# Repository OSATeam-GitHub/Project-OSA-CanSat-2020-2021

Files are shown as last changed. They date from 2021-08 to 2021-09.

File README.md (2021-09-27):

#  Project OSA

OSA a is minisatellite/ space probe the size of a can designed to participate in the ESA CanSat 2021 competition 🛰️📡. Our project is called OSA (in Polish “Opadający Satelita Atmosferyczny” is loosely translated into “Falling Atmospheric Satellite”) and team - [OSATeam](https://www.osacan.eu/)

OSA is desgined to carry out reasearches while falling in the atmospehere. Space probe can be deployed from drone, rocket or droped from certain altitude. Parachute guarantees safe landing. Primarily device measures air temperature, pressure, humidity and send it via LoRa radio to the ground station. This data is used onboard sattelite to calculate live altitude. 

The main aim for OSA is to collect five air samples🧪 for later analysis. It is done by custom-designed mechanism, that injects needle to autosealing sterile containers and pump air sample into it. 

Among other OSA has built-in GPS so after lunch it can be found easily.

CS_OSATeam2

## Tabele of contents
* [Mechanical design](#mechanical-design)
* [Electronic design](#electronic-design)
* [OSA software](#osa-software)
* [Contact](#contact)
* [Licence](#licence)
## Mechanical design
Mechanical was designed in fusion 360. The full project is available to watch with this link:
https://a360.co/3AG3GMY. 
All parts which should be 3D printed are also available above. You should use precise printer. To print them we used high-quality PLA. Inaacuracy will yield in device inoperatavity. 

### Sting System
System injects needle into container using gear and slider powered by servomechanism. Then pump inflates atmosphere into the container. In fact there is to need to use pump due to fact containers are underpressure, although puting pump into system will increase concentartion of gases. Then upper part of sting system is rotated by carousele. 



### Carousele
The carousel is designed to turn the servo and sting. It uses a stepper motor and three gears (ratio 1:1:1). The
motor does not have a centered shaft, therefore a gear system consisting of three gears has been printed on a 3D
printer. Servo gear is located in the middle and it holds the servo. On one side there is motor gear that is attached
to the [28BYJ-48 stepper motor](https://botland.com.pl/silniki-krokowe/12807-silnik-krokowy-z-przekladnia-28byj-48-5v-01a-003nm-ze-sterownikiem-uln2003.html). On the opposite side, there is support gear that makes the mechanism work with lower
backlash. Carusele is part of main-base body. It might be challenging to print therefor we additionaly added splited main-base part. Printing spearetly should be easier, after printing that way the prats should be glued togather.
Servo gear is printed in place with the base of the case as one part. It is mounted on the round body, so
it holds together. Support gear is printed as a separate part. While the base is printing the printer should be stoped at the right
height so the support gear could be manually added ( the stoping point can be set in slicer ).

karuzela napisy

### Servo mechanism
The servo mechanism converts the rotation of the motor into linear movement of the needle therefore it can be injected into the test tube.
The blocker part is additionally added to help the needle stay in place.



### Main casing body and electronic case
Both the main casing body ( main-mid ) and the electronic case are designed to be printed without any supports. They don't require as high precision as the carousel does.

## Electronic design
OSA is powered by the CanSat kit, therefore it’s fully compatible with Arduino m0. Full CanSat kit documentation can be found on the ESERO Polska page in the statute, or right [here](https://github.com/CanSatKit/Documentation). On to the mainboard, you should sold GPS module as well as the  1/2 wave long antenna. [This](https://www.changpuak.ch/electronics/yagi_uda_antenna_DL6WU.php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) calculator may be useful. 

Currently, we are working on a new PCB board for OSA. We will upload the design with the scheme soon.

OsaCan-1

### Ground station hardware
OSA ground station is simply the CanSat kit board connected with a yagi directional antenna. The mainboard should be connected by USB with PC or laptop.
It will work with any antenna which fulfils requirments (the closer to requitments the better signal:

- Frequency     :  433  MHz
- Wavelength    :  693  mm
- Rod Diameter  :  10  mm
- Boom Diameter :  20  mm
- Boom Length   :  238  mm
- d/lambda      :  0.014    ( min.: 0.002 , max.: 0.01 )
- D/lambda      :  0.029    ( min.: 0.01 , max.: 0.05 )
- Elements      :  3
- Gain          :  5.23 dBd (approx.)
- Reflector Length   : 334 mm
- Reflector Position :  0 mm
- Dipole Position    : 166 mm
- Director #1 Position : 218 mm ,  Length : 315 mm
- Distance Dipole - Dir. #1 : 52 mm 

[yagi antenna calculator](https://www.changpuak.ch/electronics/yagi_uda_antenna_DL6WU.php)

## OSA software
OSA OS is Arduino based. To make the code clean we wrote a library for controlling all OSA systems. 

Before launch, when OSA is turned on it will take measurements and calculation to establish ground altituted. Until detecting the opening of the parachute OSA will stay in the rest position. It means that the needle will be hidden between two probes so it takes less space. After detecting the opening of the parachute OSA waits about a second to stabilize and then sets current altitude as final altitude. Then it calculates five intervals on which it’s supposed to take the samples. 

Independently OSA takes measurements from all sensors every second, send it via radio and save it on SD card. Excluding pressure, temperature, humidity OSA equipped with a sensor that measures the pressure inside the pipe connected with the needle. According to that pressure we know whether the probe was taken or not. If for some reason any of the samples wasn’t taken, after taking all others OSA will come back and repeat taking those samples. OSA sends various data about the so not only do we know whether the sample was taken or not, but also exactly the altitude it started and finished taking. Also, the altitude at which the parachute was opened is saved.

OSA encodes data which is send via radio, otherwise buffor would have stucked. 

## Contact
📫 We are opened to suggestions and collaboration. Contact us!
- https://www.facebook.com/osacan.eu/
- https://www.instagram.com/osateam_cansat/
- osacansat@gmail.com
- @OSATeam_CanSat

## Licence
Copyright (C)  2020 Project OSA.

This project is free software and hardware: you can redistribute it and/or modify
    it under the terms of the GNU General Public License as published by
    the Free Software Foundation, either version 3 of the License, or
   any later version.

   This program is distributed in the hope that it will be useful,
    but WITHOUT ANY WARRANTY; without even the implied warranty of
    MERCHANTABILITY or FITNESS FOR A PARTICULAR PURPOSE.  See the
    GNU General Public License for more details.

   You should have received a copy of the GNU General Public License
    along with this program.  If not, see <https://www.gnu.org/licenses/>.
    
<!---
OSATeam-GitHub/OSATeam-GitHub is a ✨ special ✨ repository because its `README.md` (this file) appears on your GitHub profile.
You can click the Preview link to take a look at your changes.
--->

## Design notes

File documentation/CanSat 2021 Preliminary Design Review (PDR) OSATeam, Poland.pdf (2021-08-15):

## CanSat 2021 Preliminary Design Review (PDR) OSATeam, Poland

VIII Prywatne Akademickie Liceum Ogólnokształcące w Krakowie

TABLE OF CONTENTS

CHANGELOG | 2
INTRODUCTION | 2
Team presentation | 2
Team organisation and roles | 2
Mission objectives | 3
Cansat Description | 3
Mission overview | 4
Mechanical/structural design | 5
Carousel | 5
Servomechanism | 5
Pumping System | 6
Probes | 6
Casing | 7
Electrical design | 7
General architecture | 7
Primary mission devices | 8
Secondary mission devices | 8
Electrical scheme | 9
Power supply | 10
Communication system | 10
Transceiver part of OSACan | 10
Ground Receiving Station | 10
Software design | 12
Recovery system | 14
Ground support Equipment | 15
Laptop | 15
Ground receiving station | 15
Chromatograph | 15
Basic set of tool and spare parts | 15
TEST CAMPAIGN | 15
Primary mission tests | 15
Measurement tests | 15
Data download tests | 16
Sending/receiving tests | 16
Secondary mission tests | 16
Measurement tests | 16
Sting System tests | 16
Endurance tests | 16
SD card test: | 17
Tests of recovery system | 17
Communication system range tests | 17
Energy budget tests | 17
Test equipment: | 17
Project Planning | 18
Time schedule | 18
Task list | 19
Resource cost estimation | 19
Budget | 19
External support | 20
Outreach programme | 20
CanSat characteristics | 20

### 1. CHANGELOG

- One member of OSATeam resigned. The team has now 4 members and faculty advisor.

### 2. INTRODUCTION

2.1. Team presentation
OSA (in Polish “Opadający Satelita Atmosferyczny” is loosely translated into “Falling Atmospheric Satellite”) is a project of 4 students from one class out from one of Cracow’s high schools, who decided that, apart from school, they wanted to take on a serious project. Together, they decided to take part in the CanSat competition.
2.2. Team organisation and roles

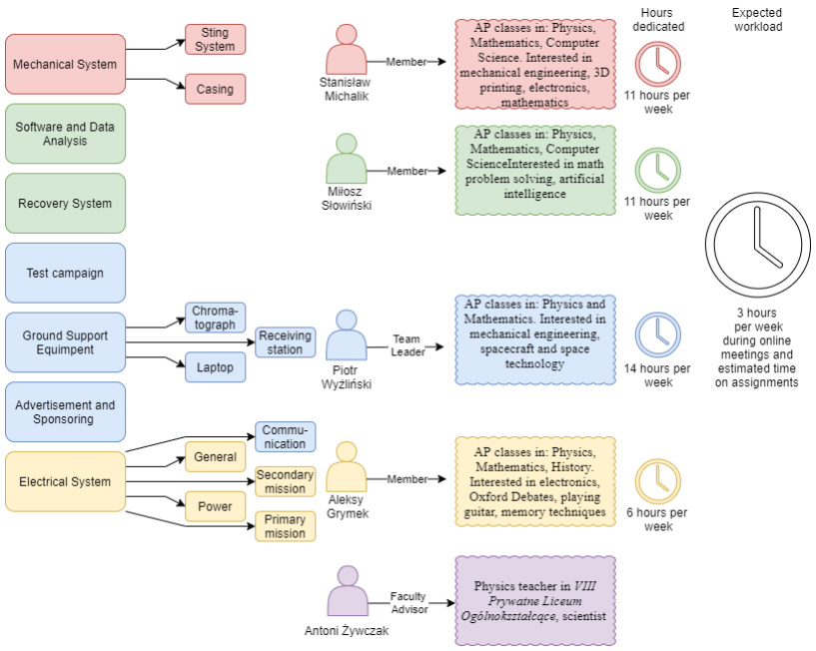
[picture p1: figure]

figure 1

2.3. Mission objectives
CanSat's primary mission is to measure the pressure and the temperature of the atmosphere during its descent and to send those measurements to a radio ground station every second. These data will be simultaneously saved in the local CanSat's memory so that it can be analyzed after the satellite lands.
The data from the primary mission will be used to calculate the height from which the CanSat will have been dropped and to calculate live altitude, and hence the speed and the time of the descent. Based on these calculations, there will be adjusted times when the next atmosphere samples are going to be collected (The first sample will be taken when the descent begins. We plan to decide if it will be detected by an accelerometer or by a different device)

The satellite will also provide the GPS location, necessary to locate CanSat after landing. Additional data related to the measurement process itself will be collected at the time of sampling, that is recording initial pressure in tanks, final pressure, filling time of tanks and diagnostic data of the filling mechanism. After analysis, this data will be used to control the filling process. At least 6 atmospheric sample containers are expected to be filled and delivered to ground, and process related data recorded.

The second mission was inspired by information from a recent Venus study, which detected phosphine that could indicate that there was life on this planet. OSATeam wants to test the Earth's atmosphere sampling system so that later a similar solution could be applied to a real mission.

The purpose of our second mission is to show that it is possible to collect samples without building satellites equipped with expensive and heavy research equipment, instead, samples can be effectively collected to be analyzed in an external specialized laboratory. Instead of investing in satellites with multiple sensors, you can invest in building many cheap satellites that collect valuable material for later analysis. The mission aims to demonstrate that this is realistic and that samples can be collected and safely delivered this way.

To ensure the success of the mission, the following goals must be met:

- Recovery system: the parachute must open and ensure a safe CanSat landing
- Electronic system and mechanical structure must work: after flight conditions (rocket acceleration),during descent (changes in pressure, temperature, humidity) and survive landing (impact)
- Sampling system: it must be hermetic, keep the tanks ariditile until sampling, it must not be damaged,
- Communication system: must ensure at least one-way communication (satellite -> ground station) during the flight and after landing,
- Software: must correctly implement the assumed algorithm, save all delivered data and send it by radio.
- Power supply system: must be safe, the energy reserve must be sufficient for the assumed number of working hours.

Optionally, samples collected during the tests will be tested for their composition in external laboratories. The analysis of the Earth's atmosphere could, for example, show that air pollutants (carbon dioxide, methane, ozone, freons, microplastics) can be detected in the air not only at the Earth's surface, and that the amount of pollutants varies depending on air humidity, altitude.

### 3. CANSAT DESCRIPTION

3.1. Mission overview
The OSACan is designed to be launched and dropped from a rocket or drone from an altitude of 500-2500 meters. After equalizing the forces, CanSat should drop at a speed of about 6 meters per second. The most important task of CanSat is to collect atmospheric samples into sealed containers while falling, using a sampling and filling mechanism at various heights. The samples are meant to be safely delivered to Earth, which requires proper protection of the probes against damage or leakage.

CanSat will descend on a parachute that will expand spontaneously as soon as it is dropped out of a rocket or a drone.

The satellite will be equipped with sensors to measure the parameters of the atmosphere outside the satellite (pressure, temperature and air humidity) and the parameters of the collected samples (pressure in the tank). The on-board computer will be responsible for the acquisition of data from sensors, their recording on the SD card and control of the radio communication system. It will also be responsible for starting and checking the air filling system for containers.

The radio communication system is designed to send these data at least once a second using a radio transmitter to the ground station, both during descent and after landing.

The GNSS module connected to the on-board computer will provide information about the current CanSat position based on the reception of GPS, Galileo or Glonass signals. The signal will be transmitted for at least 5 hours to make it easier to find CanSat after landing.

The Mechanical Subsystem (sampling and probe filling) is a key element of the second mission. A special sting system has been designed to fulfil the purpose of filling. An atmosphere sample at a certain altitude will be sucked from the outside of the CanSat by a gas pump. The gas, compressed to about 0.5 atm, will be forced into the vacuum tube by means of a needle piercing the sealed stopper. Several test tubes will be arranged around the CanSat circumference so that samples at atmospheres of different heights can be collected. In order to fill the next tube, a rotating system (the so-called carousel) was designed, driven by a stepper motor. The vertical position of the needle will be servo-controlled. The moment the tube is full will be identified by the pressure sensor. The mechanical subsystem is controlled by the Microcontroller Subsystem based on CanSat Kit pcba and additional pcba shield. All are powered by battery and Power Supply System. The microcontroller subsystem sends data to Ground Receiving Station using the LoRa radio module. Block diagram (figure 2) (https://drive.google.com/file/d/1fHhHfOO-vB5NrV_i7cEuDcGI7dE_luFc/view?usp=sharing) presents the proposed architecture of the whole system.

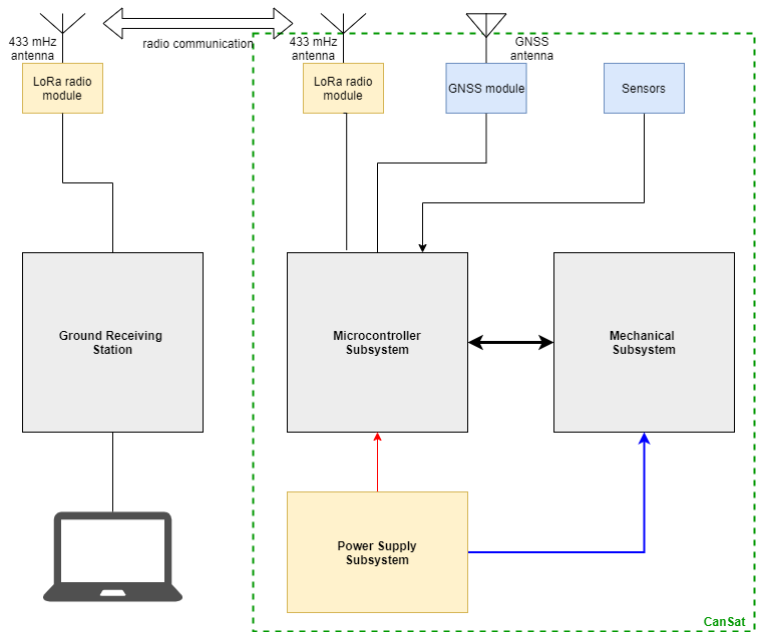
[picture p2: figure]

figure 2 (https://drive.google.com/file/d/1fHhHfOO-vB5NrV_i7cEuDcGI7dE_luFc/view?usp=sharing)

3.2. Mechanical/structural design

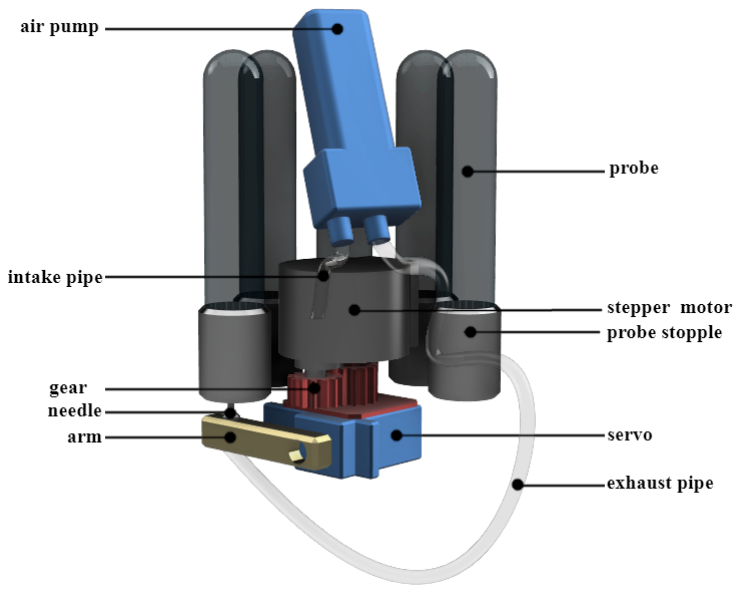
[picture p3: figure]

Figure 3 presents the Sting System. A pump will be used to collect air samples. Its inlet will lead to the outside of the CanSat and its outlet will lead to the needle. The needle will be driven into the test tubes by a servo with a special arm. To fill another tube, the servo will be rotated by a stepper motor.

← figure 3

3.2.1. Carousel
The carousel (figure 4) is designed to turn the servo. It uses a stepper motor and a gear. The motor does not have a centered shaft, therefore a gear consisting of two gears will be printed on a 3D printer.
28BYJ-48 stepper motor (https://botland.com.pl/pl/silniki-krokowe/3480-silnik-krokowy-z-przekladnia-28byj-48-5v-01a-003nm-ze-sterownikiem-uln2003-5903351241458.html) (figure 5): It was chosen due to the fact that it is the smallest stepper motor on the market with low voltage supply in a reasonable price range in the shape of a cylinder.
- Supply voltage: 5 VDC
- Current consumption per coil: 100 mA
- Number of phases: 4
- Gear: 64: 1
- Number of steps per full revolution: 64
- Rotation angle per step: 5.625 °
- Torque: 0.3 kg * cm (0.03 Nm)
- Frequency: 100Hz
- Resistance: 50? ± 7%
- Weight: 35g
- Price: 1.94 €
The motor is pressed onto the body, also holding the test tubes around it (figure 6).

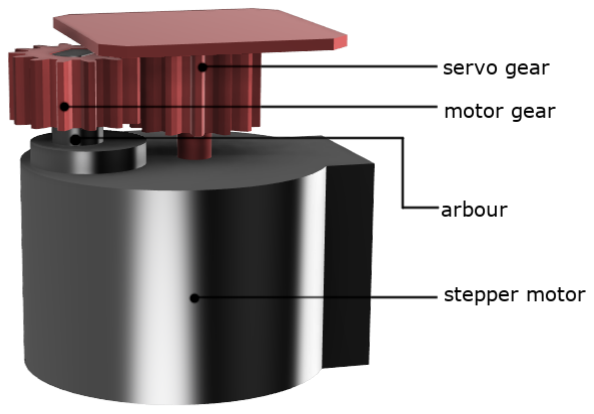
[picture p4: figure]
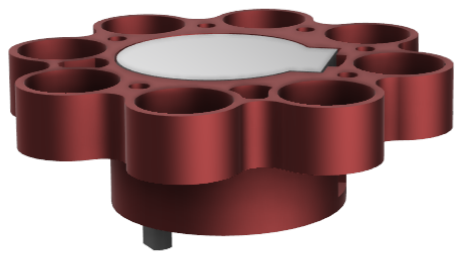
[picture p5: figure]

figure 4 | figure 5 | figure 6
3.2.2. Servomechanism
The servomechanism (figure 7) is designed to stick the needle into the next test tubes. The main part is a micro servo that moves the arm along with the needle, which is connected to the pump by a rubber tube. The micro servo will be glued to one of the gears (figure 8).
Servo Hitec HS-55 - micro (https://botland.com.pl/pl/serwa-typu-micro/578-serwo-hitec-hs-55-micro.html) (figure 9): it was chosen for its low supply voltage, high quality and reliability, extreme accuracy, metal gears and very small dimensions.
- Supply voltage: 4.8 V to 6.0 V
- Range of motion: 0° to 180°
- Dimensions: 23 x 12 x 24 mm
- Cable length: 160 mm
- Weight: 8 g
- Parameters for 4.8 V:
- Power consumption:
- 5.5 mA - idle state
- 150 mA - movement without load
- Torque: 1.1 kg * cm (0.108 Nm)
- Speed: 0.17 sec / 60 °
- Price: 12.91 €

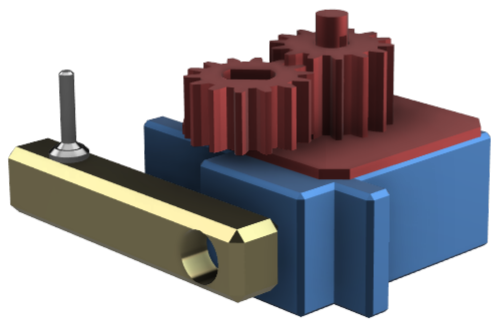
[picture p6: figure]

figure 7 | figure 8 | figure 9
3.2.3. Pumping System
The pumping (figure 10) system is designed to collect an air sample at a specific height. One inlet gas is withdrawn and the outlet is blown into the tube through the needle.
Boden Micro Pump BD-1004BV (https://www.alibaba.com/product-detail/-50kpa-0-6LPM-mini-air_62124175584.html) (figure 11): The pump has a pressure of approx. 0.5 atmosphere. It has been pre-selected due to its small dimensions, and two outlets, one taking in air, the other blowing it out.
- Pressure: -50kpa, Low Pressure
- Voltage: 3V / 6 VDC
- Power: 2 ~ 3W
- Rated Volt: DC3.0V
- Current: ≤400mA
- Flow: ≥0.6LPM
- Inflating time: ≤30S (100CC)
- Noise: ≤60dB (A)
- Dimension: 47mm x 21mm x 12mm
- Weight: 20g
- Price: 8.44 €
The pump will be attached to the body as shown in figure 12 (beveled as it fits diagonally), and the air supplied and exhausted is as shown in figure 13.

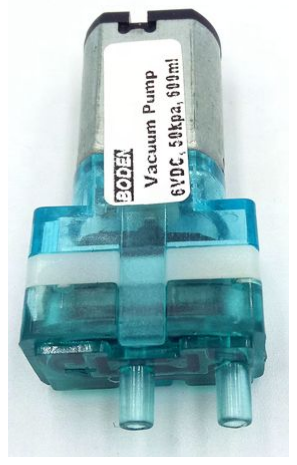
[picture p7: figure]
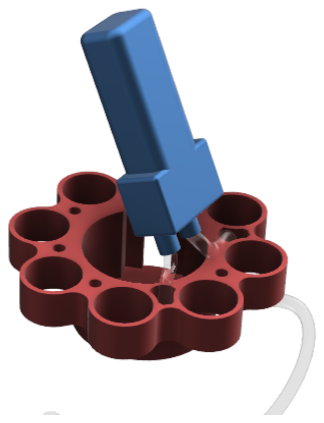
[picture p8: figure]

figure 10 | figure 11 | figure 12 | figure 13
3.2.4. Probes
They are a container for air samples. They are made of thin glass and plastic closures. The Vacumed® probówka neutralna na 4 ml krwi 13x75mm jałowa, korek czerwony (https://www.equimed.com.pl/katalog/15-zamkniety-system-pobierania-krwi-vacumed/) (figure 14) model was chosen. Tubes are sterile, vacuum sealed, and used in blood collection systems. Filling is done by puncturing the stopper with a needle. After removing the needle, the hole seals itself. Their price is: 9.68 € for 100 pieces. It is important that the container (test tube) has no contamination, it should be as sterile as possible and empty of gases. The test tubes will be attached to the casing by pressing (figure 15 & 16), so that they can be easily removed and the samples can be examined. To replace with new tanks, just remove the casing, take out the old ones and replace with new ones.

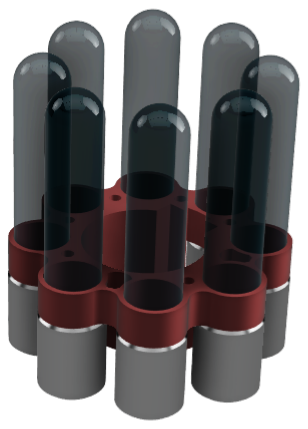
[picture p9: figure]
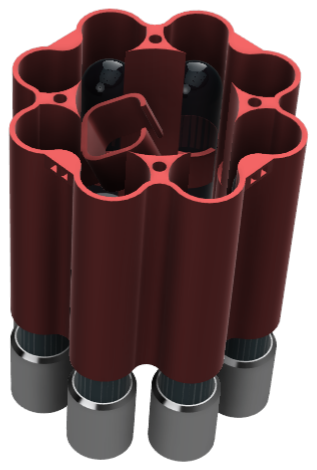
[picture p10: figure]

figure 14 | figure 15 | figure 16
3.2.5. Casing
The entire casing (figure 17) will be printed on a 3D printer, in addition, the most delicate elements will be additionally secured with a sponge.
The casing is designed to:
- provide the basis for mounting the satellite components,
- protect mechanical and electronic components from damage,
- prevent CanSat elements from moving, protect them from high G-force.
- protect the test tubes from breaking and, if they do break, protect them from injuring people who find OSACan after landing
- provide quick access to the CanSat interior, including the battery
- enable any mechanical elements to operate freely,
- protect the inside of the satellite from outside conditions (temperature, humidity, air momentum when falling)
The casing has no bottom, as more space was needed for the movement of the arm with the servo.Figures 18, 19, 20 show 3 parts of casing. Reason for using 3 different parts is to ease access to inner elements. All mechanical and electrical components will be inside the main part as well as above CanSat Kit.

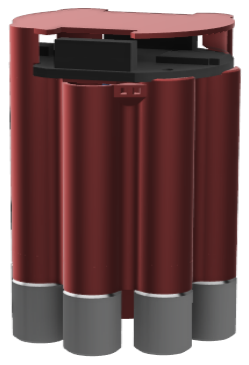
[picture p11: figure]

figure 17

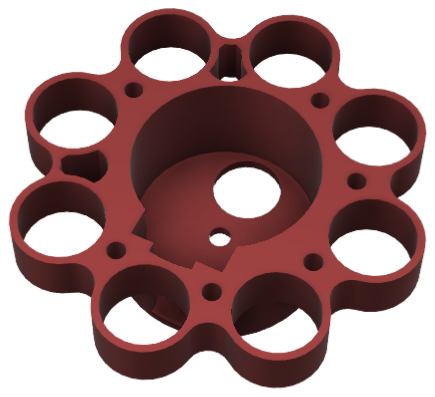
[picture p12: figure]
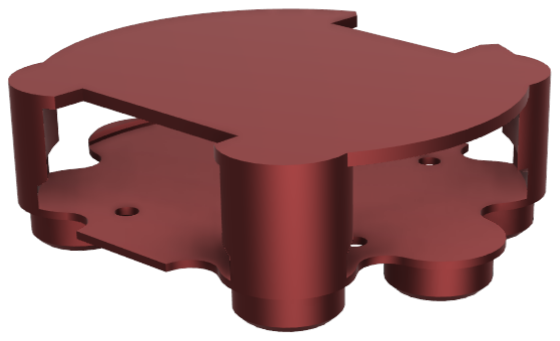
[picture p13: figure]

figure 18 | figure 19 | figure 20
3.2.6. Electrical design

### 3.2.6.1. General architecture

The general architecture is presented on the following diagram. The concept of the microcontroller subsystem is based on ready-to-use CanSat Kit (https://github.com/CanSatKit/Documentation/blob/master/CanSatKit_User_Manual_PL.pdf) and pcba shield with additional elements.Elements are marked in:

- yellow - located in the main pcba (CanSat Kit)
- blue - pcba shield (to be developed)
- violet - outside pcba, mounted directly to the housing body.

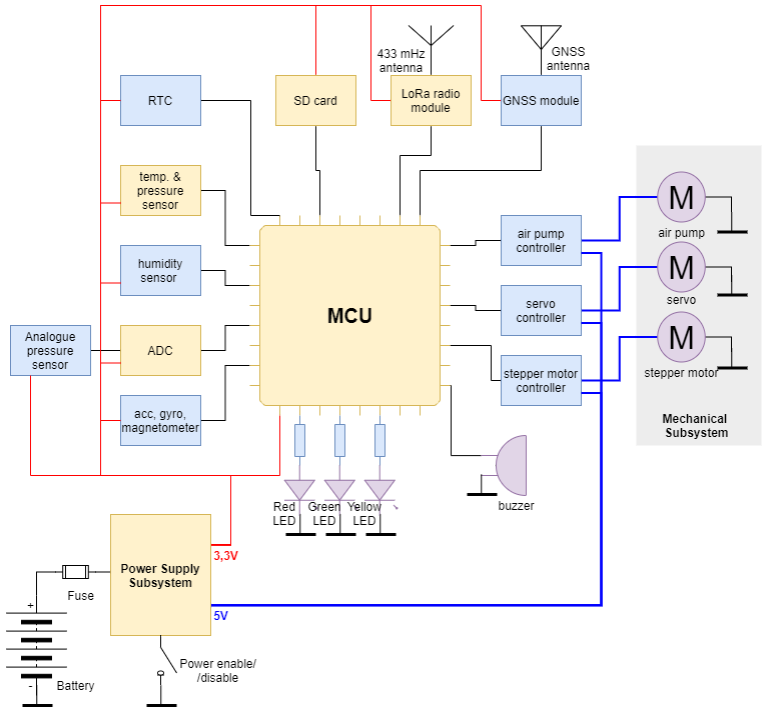
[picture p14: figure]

figure 21 (https://drive.google.com/file/d/1fHhHfOO-vB5NrV_i7cEuDcGI7dE_luFc/view?usp=sharing)

Some elements are selected, other elements will be selected during the prototype phase.

3.2.6.2. Primary mission devices
- Temperature sensor: Model - LM 35 (https://allegro.pl/oferta/lm35dz-to-92-analogowy-czujnik-temperatury-0-100c-9526881192) (figure 22)
- Used for measuring temperature at certain height
- Temperature range - (-55*C)-150*C, Measuring in Celsius, Accuracy to 0,5*C, Voltage: 4V-30V
- We are using this particular one because it is attached to the integrated circuit
- Price : 0,33 €
- Atmospheric Pressure sensor: Model - BMP280 (https://allegro.pl/oferta/bme280-czujnik-temperatury-wilgotnosci-cisnienia-7954651090?ev_adgr=Inne) (figure 23)
- Used for measuring atmospheric pressure at certain height
- Atmospheric pressure range - 300-1100 hPa, Accuracy to 1hPa, Voltage 3,3 V
- We are using this particular one because it is attached to the integrated circuit
- Price : 0.52 €
- Radio module: model SX1278 RA-02 LoRa 433MHz
- (described in 3.2.6.5.1, communication system Transceiver part of OSACan)
3.2.6.3. Secondary mission devices
- Pressure sensor: (https://botland.com.pl/pl/czujniki-cisnienia/959-mpxm2202as-analogowy-czujnik-cisnienia-200kpa.html) model - MPXM2202AS (figure 24)
- Output Type - Analog, Pressure Range (kPa) 0-200, Pressure Rating (MAX) (psi) - 29, Supply voltage [typ] (V) - 10.
- It’s purpose is to measure pressure inside the probes
- Price : 9,60€

- Humidity Sensor: model - HIH-4030 (https://allegro.pl/oferta/hih-4030-analogowy-czujnik-wilgotnosci-9737189806?ev_adgr=Inne) (figure 25)
- 4-5.8VDC voltage supply, All pins broken out to a 0.1" pitch header, Laser trimmed interchangeability, Low power design, typical current draw of only 200μA ,Enhanced accuracy, Fast response time, Stable, low drift performance, 0.75 x 0.30 " (19.05 x 7.62 mm .
- It is very small, durable and quite enough accurate
- Its purpose is to measure air humidity inside the probes
- Price : 23.99€
- Accelerometer, magnetometer, gyroscope - LSM9DS1 (https://botland.com.pl/pl/czujniki-9dof-imu/7191-lsm9ds1-sensor-stick-imu-9dof-3-osiowy-akcelerometr-zyroskop-i-magnetometr-i2c-sparkfun-sen-13944.html) (figure 26)
- Used for checking weather the parachute is open or not
- Voltage: 1,9V - 3,6 V
- 3 axis x,y,z
- Boden Micro Pump BD-1004BV
- (described in Pumping System)
- Servo Hitec HS-55 - micro
- (described in Servomechanism)
- stepper motor - 28BYJ-48 (https://botland.com.pl/pl/silniki-krokowe/3480-silnik-krokowy-z-przekladnia-28byj-48-5v-01a-003nm-ze-sterownikiem-uln2003-5903351241458.html)
- (described in Carousel)
- Location system
- not selected yet ; dependable on other variables
figure 22 | figure 23 | figure 24 | figure 25 | figure 26
3.2.6.4. Electrical scheme We started drawing the electrical schematic of pcba shield in KiCad software. The preliminary version is presented in the figure 22

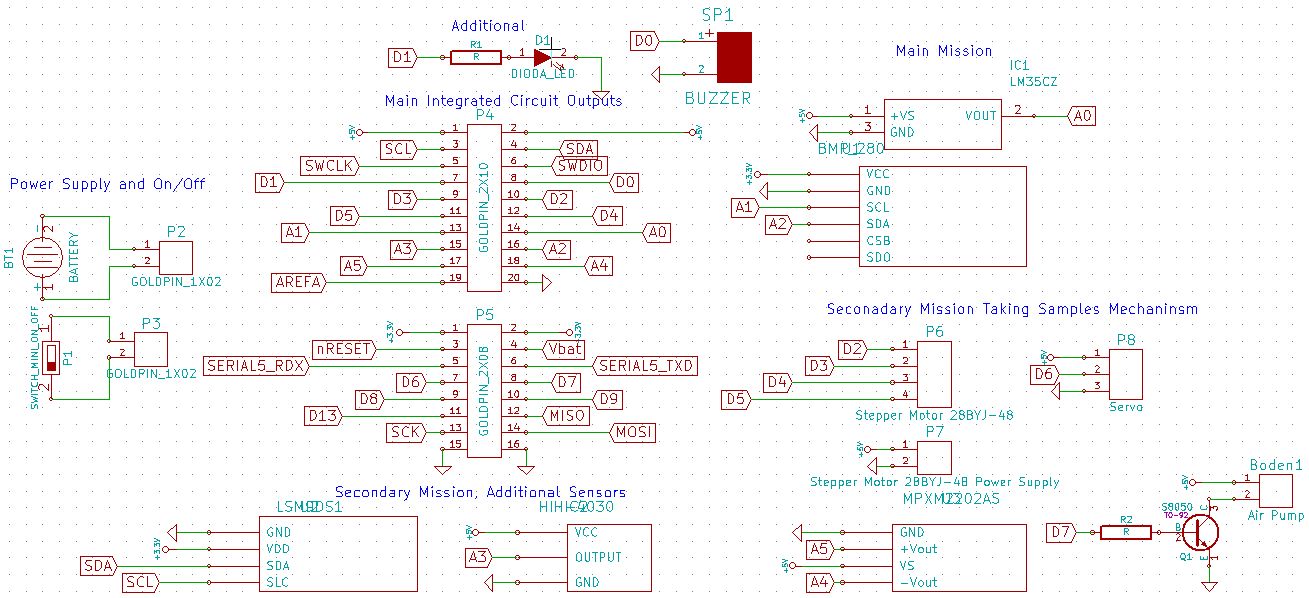
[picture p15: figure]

figure 27

3.2.6.5. Power supply

Batteries will be selected in the next phase of the competition to fit our demands after we conduct tests regarding the electrical modules.

### 3.2.6.6. Communication system

The following assumptions were made for the communication system:
- communication between the satellite and the ground receiving station is one-way, that is from CanSAT to the ground station
- communication takes place in the 433 MHz public band
- the radio layer of communication will take place with the use of ready-made LoRa modules
- power cannot exceed 20 dbm (as required)
- the satellite antenna must fit in the assumed dimensions of the satellite, it must extend to a certain length along with the parachute deployment.
To achieve the goal it is necessary:
- Equipping the satellite with a LoRa micro-transmitter with an antenna.
- Building a ground receiving station with a directional antenna.

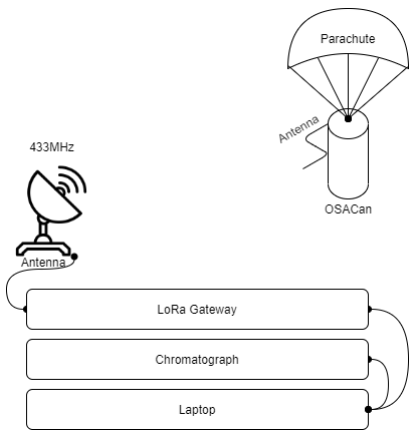
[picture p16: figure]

figure 28

### 3.2.6.6.1. Transceiver part of OSACan

SX1278 RA-02 LoRa 433MHz module - installed in CanSat Kit:
- Range: 10-15km
- Sensitivity: -148dBm
- Transmission speed: up to 300kbps
- Working frequency: -148dBm
- Supply voltage and work: 1.8-3.7v
- Working temperature: -40- + 80 ℃
- Communication method: LoRa
- RF transmitter power: + 20dBm-100mW
- Communication: SPI
- Price: Included in the CanSat Kit price

### 3.2.6.6.2. Ground Receiving Station

will consist of:
- LoRa Gateway
- directional antenna,
- antenna cable (50 Ohm)
- the necessary software ensuring the receipt of messages, LoRa Gateway

A ready-made LoRa Gateway solution can be used as the receiving device. There are many such devices on the market, the final purchase decision will be made depending on availability at the time of implementation and delivery time. Examples of available devices:

LoStik open source USB LoRa device by Ronoth (https://www.tindie.com/products/steven/lostik-open-source-usb-lorar-device/) (figure 28)
LoStik by Ronoth is an easy to use, open source USB LoRa device. It was chosen because of the best documentation of all available devices, open source software and programmable leds.
- Frequency Range:433/868Mhz
- Connectivity: USB 2.0
- Power Consumption: 140 mA typical TX, 20 mA idle (with power LED)
- Dimensions:80 mm x 25 mm x 12 mm
- Receiver Sensitivity: down to -146 dBm
- TX Power: adjustable up to +14 dBm
- Chip: Microchip RN2483
- Range: 5-15 km
- Price: 38.92 €
iFrgoLab LoRa USB gateway (http://www.ifroglab.com/en/?product=ifroglab-lora-usb) (figure 29)
for Raspberry Pi, Linux, Windows, Mac LoRa, LoRaWAN, IOT, 433/868Mhz, SPI Data Interface Sensitivity: -137dBm, Output Power: +20dBm is alternative for USB LoRa device by Ronoth.
- Frequency Range: 433/868/900/915 Mhz
- Connectivity:USB 2.0
- Power Consumption:unknown
- Dimensions: unknown
- Receiver Sensitivity: down to -137 dBm
- TX Power: adjustable up to +20.0 dBm
- Chip: Semtech SX1272
- Range: up to 15 km
- Prize: 50.69 €
Both LoRa gateway devices are connected to the USB 2.0 port and can work with Linux / Windows operating systems. If you need to bring the gateway closer to the antenna, you can use a USB extension cable for example:
Delock USB 10.0m czarny (https://www.komputronik.pl/product/179893/delock-usb-10-0m-czarny.html) (figure 30)
A USB extension cable is needed to connect LoStik to a laptop. It was chosen due to its availability in the country, length and the appropriate price and quality.
- Standard: USB
- Ending 1:1 x USB 2.0 (typ A)
- Ending 2: 1 x USB 2.0 gniazdo (typ A)
- Length: 10 m
- Price: 15.25 €
Gateways are standard equipped with a broadband omnidirectional antenna, which is most likely to have a poor signal gain for communication with CanSAT. The antenna is not permanently attached, an extension cable with an impedance of 50 Ohm can be connected to the derived SMA antenna connector, to which the directional antenna will be connected:
Delock RP-SMA male / RP-SMA female 2m black (https://www.conrad.pl/p/kabel-przedluzajacy-anteny-wifi-delock-1x-zlacze-meskie-rp-sma-1x-zlacze-zenskie-rp-sma-200-m-czarny-649734) (figure 31): Flexible and easy-to-use antenna extension cable allows you to position the antenna anywhere. The HF cable is characterized by its low-loss.
figure 28 | photo 29 | photo 30 | photo 31

Ground station directional antenna
A sensitive receiving circuit is required over long distances. One way to increase the sensitivity is to use an antenna with a good gain. Antennas with directional characteristics work well in such applications, for example the Yagi antenna: (https://pl.aliexpress.com/i/32958565058.html)
figure 32 | figure 33

We plan to build such an antenna ourselves. It will be built of a boom made of a rectangular metal profile 10 x 10 [mm], it will be equipped with transverse active elements made of aluminum tube 6x6 [mm] and folded dipoles also made of aluminum tube 6x6 [mm]. The construction and dimensions will be calculated using “Yadi Una Antenna Calculator”. (https://www.changpuak.ch/electronics/yagi_uda_antenna_DL6WU.php) For example, for a 6-element antenna we need a mast length of approximately 0.7 m and it will be possible to obtain a gain of approximately 9 dB.

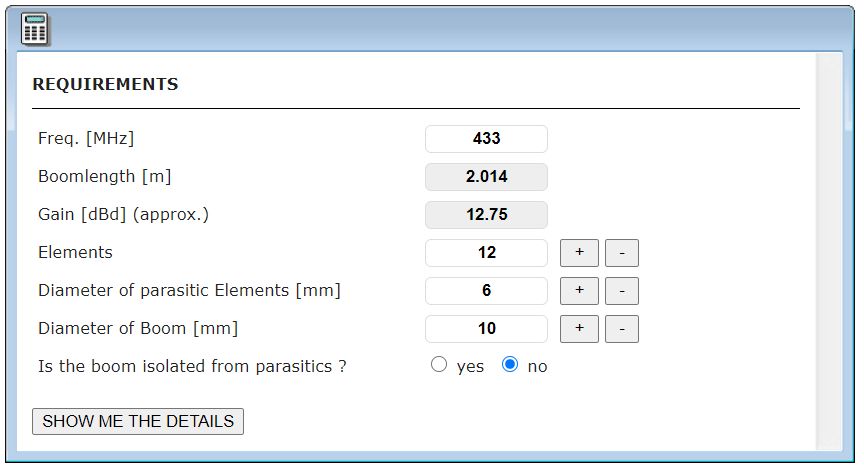
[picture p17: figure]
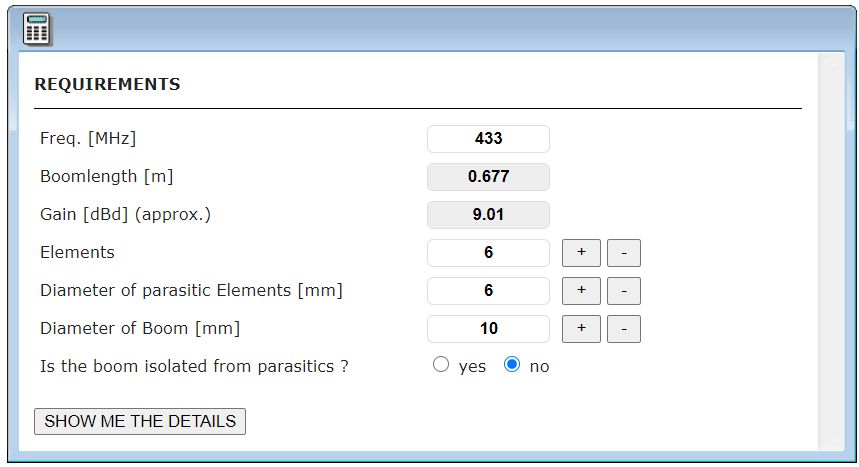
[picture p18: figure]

figure 34 | figure 35

A gain of 12 dB requires a 12-element antenna with a length of 2 m.
The CJU type antennas also have very good parameters, which we can also try to make ourselves. (https://pd0g.wordpress.com/2017/04/17/cju-or-ioio-antenna-for-70cm/)

Satellite radio system
The transmitting antenna in the simplest case is a wire of appropriate length, being the wavelength λ or its fraction (eg λ / 2, λ / 4…). It is important to tune the antenna, that is, cut the cable to the correct length. For a wave with a frequency of 433 MHz we have a wavelength according to the formula
λ =c*T = c/f
where c = 299 792 458 [m / s] is the speed of light, T is the period, f = 433 [MHz] is the frequency
which gives the following possibilities:
- for a full-wave antenna (λ) we have the antenna length 69.24 [cm]
- for a half-wave antenna (λ / 2) we have the antenna length of 34.62 [cm]
- for a quarter-wave antenna (λ / 4) we have the length of the antenna 17.31 [cm]
It will be best to use a full-wave or half-wave antenna, we anticipate that it will develop along with the parachute lines. The length of the antenna will be finally selected during the implementation of the recovery system (parachute).
3.3. Software design
Software should cover the support of CanSat Kit Hw v.1.4 and our additional shield with planned pheripherials. Our team will develop the software on microcontroller using the Arduino toolchain.
The preliminary software architecture is described in figure 36: (https://drive.google.com/file/d/1Gn2BvjH5cnhchuZfHHeqSZyn8iJGMW5z/view?usp=sharing)
- state-1: CanSat in this state is waiting for deployment. No primary and secondary activities, due to battery capacity limitation. Main loop is waiting for trigger signal (parachute deployment)

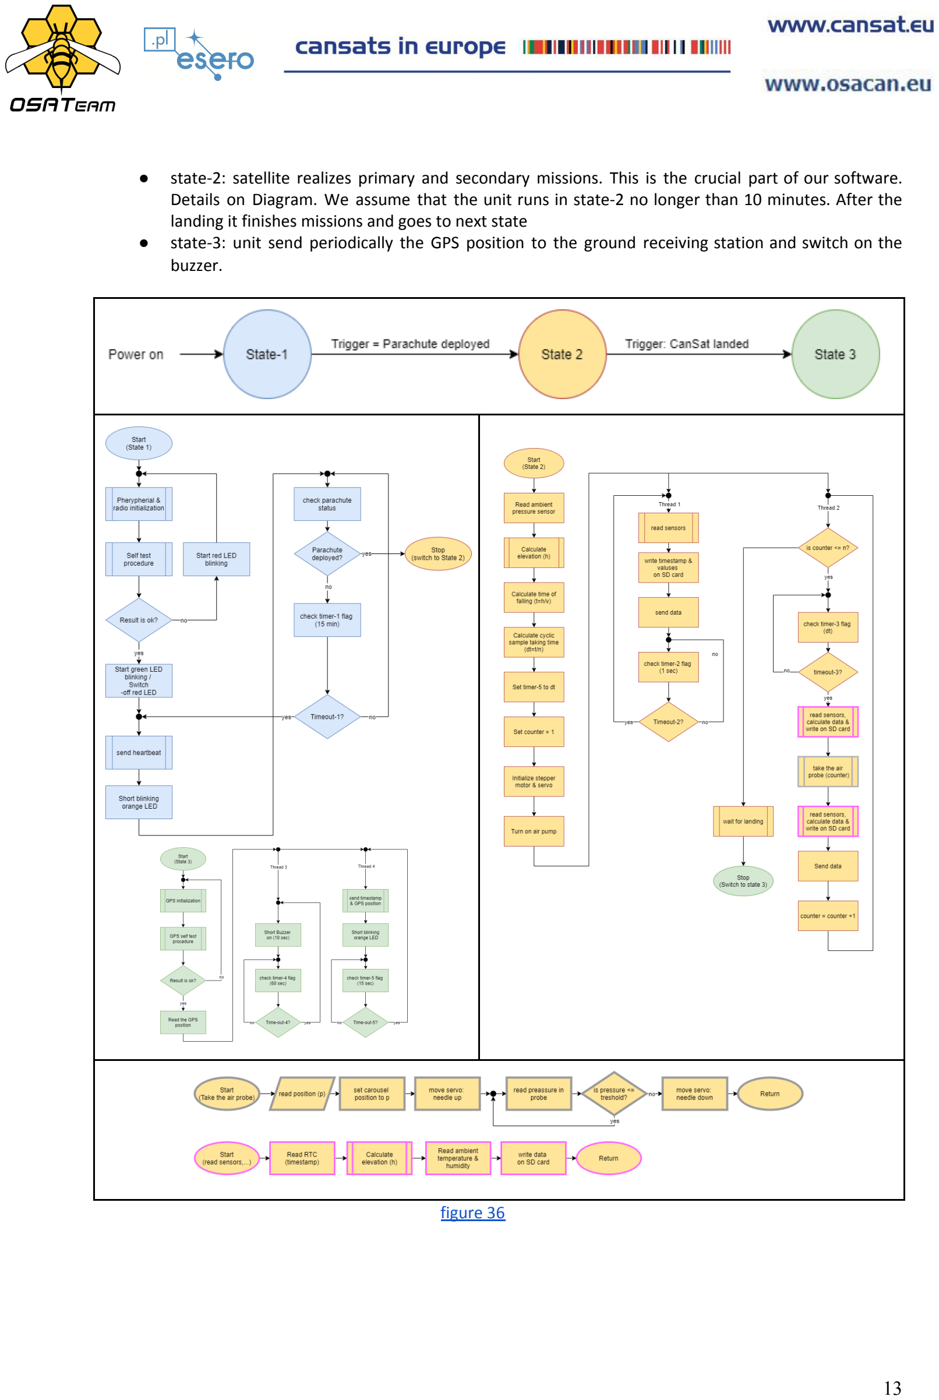
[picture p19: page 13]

- state-2: satellite realizes primary and secondary missions. This is the crucial part of our software. Details on Diagram. We assume that the unit runs in state-2 no longer than 10 minutes. After the landing it finishes missions and goes to next state
- state-3: unit send periodically the GPS position to the ground receiving station and switch on the buzzer.

figure 36 (https://drive.google.com/file/d/1Gn2BvjH5cnhchuZfHHeqSZyn8iJGMW5z/view?usp=sharing)

3.4. Recovery system

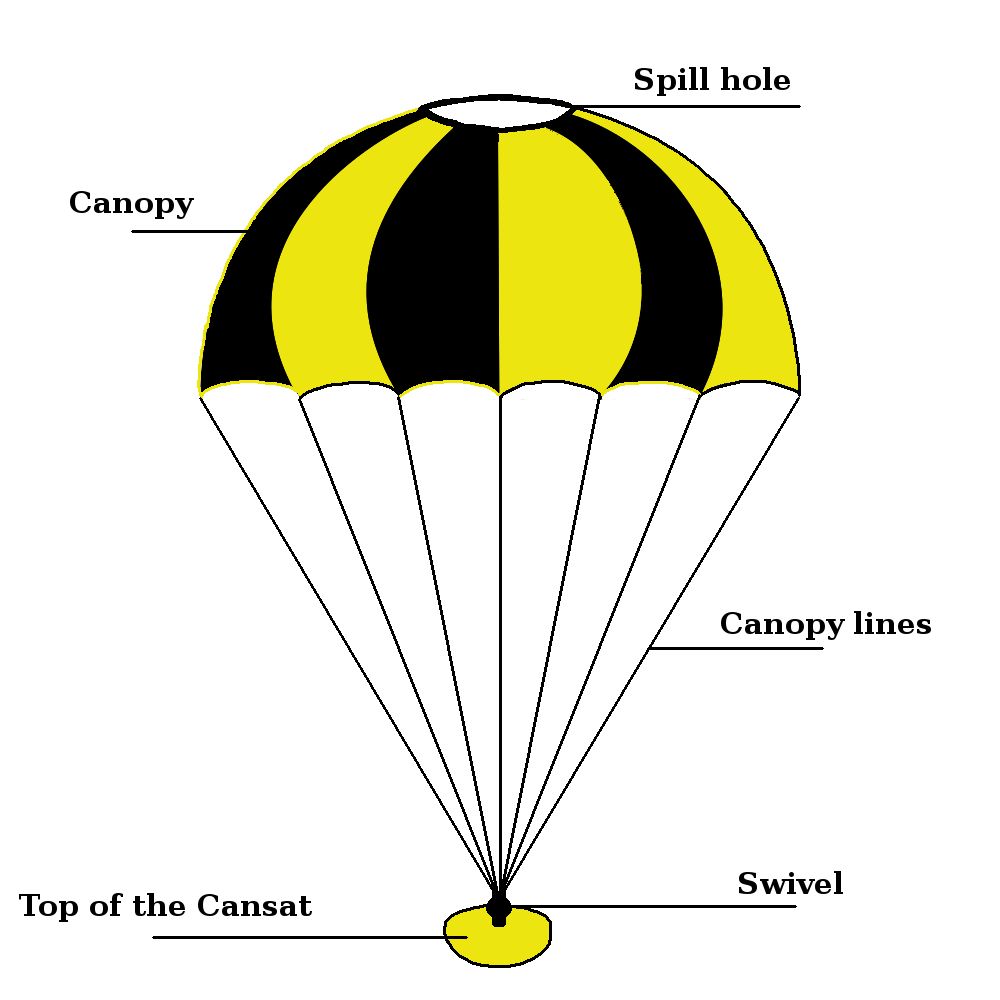
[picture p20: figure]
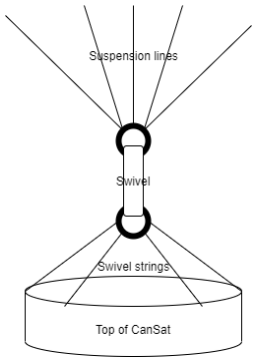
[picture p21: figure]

figure 37 | figure 38

As a recovery system we have decided on using a parachute. The drag force, which can be easily calculated, will allow our precious cansat to fall with targeted speed. We did not want our cansat to drift too far into the distance, however we needed for our probes to land relatively safely so we decided on terminal velocity equal eight meters per second. Using the terminal speed equation we can figure out the area of the chute. Out of the most popular parachute canopies such as square, cross or round canopy the last has the highest drag coefficient thus will assure the lowest area. In the middle of the canopy there will be located a spill hole that will keep the chute from tilting sideways. The ratio between spill hole area and canopy area will measure 1/20. Furthermore we will be connecting canopy lines to the cansat using a ball bearing swivel that will help prevent line entanglement. The length of the canopy will be 20% longer than the canopy radius.

- Air density approximation ρ = 1.225
[kgm3]
- Gravity acceleration approximation g = 9.81 [ms2]
- Cansat mass approximation m = 0.35 [kg]
- Drag coefficient for round type canopy Cd = 1.3
- Terminal velocity of Cansat V = 8 [ms]
- Pi constant approximation π = 3.1415
- A - area of the canopy
- R1 - radius of the canopy
- R2 - radius of the spill hole

V = √ Cd × ρ × A
2 × m × g
A = | ;

2 × m × g
C × ρ × V d

2
A = π × (R )1

2 − π × (R )2

| 2
A = π × (R1
) | %

2 − π × (R )1

| 2 × 5
A = π × (R1

) 5%

2 × 9
R1 = √
A
0.95 × π
5% × A = π × (R )2
| 2
R2 = √ π
0.05 × A

Parachute will be made out of:
- swivel: Apogee 220# ball bearing swivel (https://www.apogeerockets.com/Building_Supplies/Parachutes_Recovery_Equipment/Swivels/200_Ball_Bearing_Swivel) (figure 39)
- weight: 4.2 [g]
- price: 3.83 €
Swivel will be hitched with 4 strings, attached to the top of CanSat (scheme 7). The reason for using a swivel is to make sure lines will not muddle.
- canopy fabric: ripstop nylon fabric (https://www.ripstop.pl/produkt/ripstop-nylon-miodowy/) 1.5 x 1.5 [m] (figure 40)
- weight: 64.42 [g/m²] - (parachute canopy itself will weight around 9[g])
- price: 9.83 €
- canopy lines: 25/50 / 100FT 550 Paracord Parachute Cord (https://www.wish.com/product/5d9ef1517da4cf30a2b74d87?from_ad=goog_shopping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) (figure 41)
- price: 0.87 €

figure 39 | figure 40 | figure 41
3.5. Ground support Equipment The ground support system will consist of the following components:
- Laptop
- A ground receiving station, consisting of:
- directional antenna,
- antenna cable (50 Ohm)
- LoRa Gateway,
- the necessary software ensuring
- the receipt of messages,
- spare battery pack for CanSat
- optional laboratory facilities
- portable chromatograph,
- data analysis software.
- basic set of tools and spare parts.
3.5.1. Laptop
Any model with Linux or Windows, suitable computing power and a USB input. It will have special software installed to present the data collected on the mission.
3.5.2. Ground receiving station (described in communication system)
3.5.3. Chromatograph
The chromatograph is a very expensive device, we are not going to buy it. We decided on borrowing it from one of the sponsors or from the university

1 2 3
| | . That is the reason we do not have a specific
model inscribed yet.
An alternative is also to deliver the collected gas samples to the sponsor's laboratory or the university (if the loan approval could not be obtained).
3.5.4. Basic set of tool and spare parts

### 4. TEST CAMPAIGN

4.1. Primary mission tests
4.1.1. Measurement tests
- pressure sensor test: this will involve exposing the used sensor to a pressure change and comparing the results with a reference device. A special pressure chamber will be used for this type of tests, from the AGH laboratory. In the event that such equipment is not accessed, the target and reference sensors will be inserted into a sealed container where the pressure will be increased by a compressor or both sensors will be taken upwards where the pressure will decrease with increasing altitude. It is estimated that the test will last 6 hours, which is the assumed maximum time that CanSat should be

1 http://www.wggios.agh.edu.pl/badania-naukowe/laboratoria-i-aparatura/laboratorium-chromatografii-gazowej/2 https://www.jagiellonskiecentruminnowacji.pl/laboratoria/laboratorium-chromatografii-i-spektrometrii-mas/
3 https://kghmcuprum.com/o-nas/zaklady-badawcze/laboratorium-zagrozen-pylowo-gazowych-i-klimatycznych-nl-3/

found after a fall. The test will be considered positive when both sensors show the same pressure without measuring errors.
- temperature sensor test: it will consist in checking whether the target device and the reference device will show the same temperature within 24 hours
4.1.2. Data download tests
- After positive results of the measurement tests, the data download system will be checked. The device will be turned on successively longer and longer periods and left for measurements. After this time, the collected data on the SD card will be validated for completeness and the occurrence of errors.
4.1.3. Sending/receiving tests
- The first test will be multiple initiation of communication (connect / disconnect). Once everything is running, the communication system will undergo a long-term test of continuously sending and receiving data one by one. It will be checked whether all the data has arrived and whether there have been any delays. Finally, the system will be tested for radio interference. Signals of a similar frequency will be sent from another transmitting device. Ultimately, this should not affect the received data, but it may introduce delays.
4.2. Secondary mission tests divided into measurements tests (pressure, humidity, location), Sting System tests, saving data to SD card tests:
4.2.1. Measurement tests
- Analogue pressure sensor test: (described in 4.1.1 - Measurement tests, pressure sensor test)
- Humidity sensor test: will be tested in an airtight container where the humidity will be increased by the evaporating water. The measurement should be the same as on the reference sensor.
- Location test: the measurement from the GNSS system will be compared to that from a smartphone.
4.2.2. Sting System tests
The test consists of a mechanical system test and general endurance tests.
- -mechanical system test:
- -stepper motor with gear in terms of precision and speed of rotation
- -the servo will be checked together with the arm. The needle should hit the rubber opening of the test tube precisely without breaking
- -pumping system: tubing system, pump and tubes must be tight. In a closed system, it will be tested whether the appropriate pressure will be achieved (0.5 atm). Additionally, it will be measured whether this pressure is obtained in a timely manner.

### 4.2.3. Endurance tests

- Drop resistance test: OSACan will be attempting a crash test. Under normal conditions, when the parachute opens, no element, including the casing, should be damaged, especially important when yanked when the parachute is unfolded as well as when hitting the ground. Also, all internal components should not move, the electronics should work continuously. To test this, CanSat prototypes will be dropped from a height sufficient to achieve the descent speed (from a tower or drone). A fall test without a parachute is also planned, from a height such as to obtain a falling speed 2-3 times faster than assumed. Optionally, it is envisaged to add a 3-axis accelerometer to the electronics board (if within budget and weight constraints) to record any G-force.
- Long-term G-force tests: during rocket transport, G-force up to 20G may occur. In order to simulate such G-force, we plan to perform an experiment consisting in placing the satellite model on a carousel or string, introducing the satellite into rapid rotation. It is possible to achieve the required overload due to the centrifugal force.

G - gravitational acceleration
ω - angular velocity
R - string length
n - quantity of rotations
t - time of rotating

G = ω R

2
G = R
Δt

2

4π n

2 2

- Shock resistance test: CanSat will be put into a special shaker (AGH equipment). Ultimately, during
| long-term shocks (tests on the order of 1 hour), no element is to be damaged, slipped out or
| significantly moved.
4.2.4. SD card test:
will be tested for correctness of writing, storing and reading data (test program)
4.3. Tests of recovery system
- Parachute deployment test: this will consist of mounting the parachute to a load equal to the weight of the CanSat, and then dropping it from ever greater heights. Initially, it will be thrown from buildings and hills. When tests at higher altitudes are required, a drone will be used to drop it, to which a specially designed CanSat detachment system will be connected. Ultimately, the parachute must fully open within the specified time. to make any possible amendments, the testing process will be recorded and analyzed on this basis.
- Parachute test for various weather conditions: parachute with the weight attached will be dropped during: rain and / or wind. The test result will be recognized as successful only if the parachute is fit for reuse
- The flight path and its speed test: The dummy-mass model during the fall will be recorded and then analized in Tracker by Physlets (https://physlets.org/tracker/?fbclid=IwAR3IaHUYn47i2sWyqmBfONZz9r2wTcv4GMQq_aQnM9EwPRvhF0ly0VO-iOo) in terms of flight stability and falling speed. Additionally, the moment of opening the parachute from the analysis should be consistent with that of the accelerometer.
4.4. Communication system range tests
- The signal strength test will be performed, whether we achieve the assumed radiation power, but also whether we do not exceed the permissible amount of emitted power as well as electromagnetic disturbances. Such tests are performed in anechoic chambers designed to measure EM (https://elektronikab2b.pl/technika/11675-kompatybilnosc-elektromagnetyczna-pomiar-emisyjnosci/strona) emissivity. The necessary measuring equipment (chamber, carrier wave generator, exposure emitter, analyzer) is beyond our reach, we intend to reach a professional laboratory (AGH, Sponsor)
- The maximum achievable range of CanSat under different conditions is measured:
- In open space - expected measurement 10 km
- in urban built-up space - expected measurement 3 km
- measurements should be consistent with the calculations of Fresnel zones (https://en.wikipedia.org/wiki/Fresnel_zone)
- Additionally, a range and communication test will be performed during: freefall, a balloon or a drone flight. Ultimately, communication with CanSat should be up to 3 km vertically, it will probably be difficult to reach this height, however based on measurements at a lower altitude and the theory of wave propagation in the atmosphere, we plan to estimate the result .
4.5. Energy budget tests
The power supply system must guarantee the supply of the entire system for the duration of the mission, according to the recommendations, we expect that the battery will last for 8 hours of operation, but we divide this time into the following periods (modes):
1. from satellite activation to deployment (Basic Mission functionality enabled) - 4 hours
2. from deployment to landing (full functionality enabled: primary + secondary mission) - up to 10 minutes (down from 2,500 km by parachute)
3. From landing to being found (Basic Mission functionality with GPS data enabled) - up to 4 hours
In order to test whether the capacity of the selected type of battery that will be determined at a later stage (https://ep.com.pl/files/9461.pdf) -is appropriate, we will perform:
- measurement of current consumption by systems and components in modes 1,2, 3 and calculation of energy consumed
- checking the actual capacity of the battery by loading it with a simulated resistive receiver
- under normal conditions
- at low temperatures (the battery
- may lose its properties)
Maximum device operating length test under real conditions, covering all 3 modes
- we assume that the battery will be discharged to a maximum of 80%, and the voltage of cells connected in series will not drop below 5V.
4.6. Test equipment:
- reference sensors (pressure x2, humidity, temperature),
- phone - gps,

- recommended sensors inside the satellite (accelerometer, battery voltage)
- voltmeter + ammeter
- Power Supply

### 5. PROJECT PLANNING

5.1. Time schedule
For the project schedule we plan to use the web Gantt tool https://app.teamgantt.com/ . The basic tasks were divided into a few week periods and planned, the effect is shown on figure 42. Main steps are:
- Ideation - finished
- Design - work-in-process
- Prototyping - work-in-process
- Tests (prototype) - to be defined (tbd) in details
- Construction (Run A) - tbd
- Test campaign (Run A) - tbd
- Construction (Run B) - tbd
- Test campaign (Run B) - tbd
- Competition - we hope to participate
Run A will be the first of our construction, probably with a set of mistakes. Run B means the second and final construction, improved after Run B. We plan to order the whole BOM twice to support both Run A and Run B. At the same time we plan to carry out activities related to:
Outreach programme:

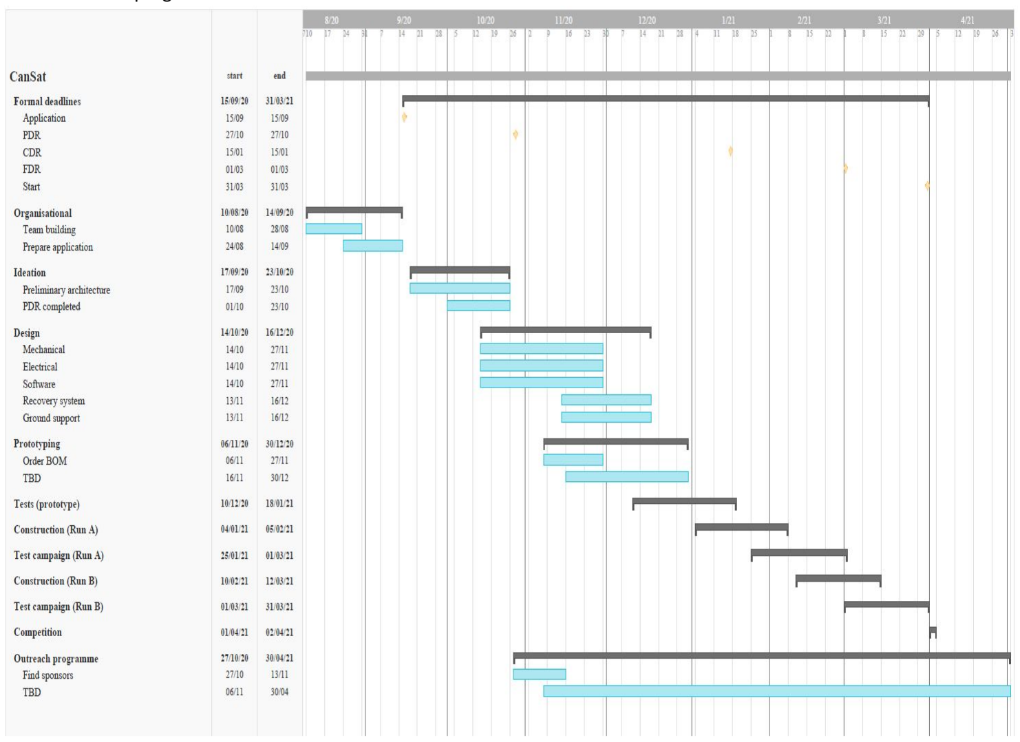
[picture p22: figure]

figure 42

5.2. Task list

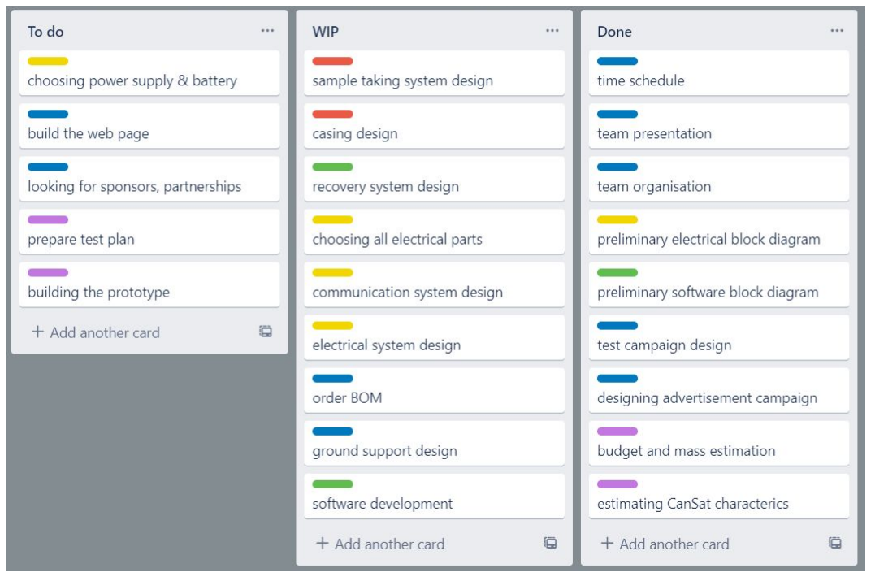
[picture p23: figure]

Figure 43
(colors refer to the figure 43. with addition of purple which is the responsibility of the whole team)
5.3. Resource cost estimation
5.3.1. Budget
Cansat: | Ground station:
- 28BYJ-48 stepper motor : 1.94 € ● motherboard - 38.19 € ● Servo Hitec HS-55 - micro - 12.91 € ● Boden Micro Pump BD-1004BV - 8.44 € ● The Vacumed® probówka neutralna na 4 ml krwi 13x75mm jałowa x 100 - 9.68 € ● Swivel- 3.83 € ● canopy fabric - 9.83 € ● canopy lines- 0.87 € ● Temperature sensor - 0.33 € ● Atmospheric Pressure sensor - 0.52 € ● Radio module - 2.47 € ● Humidity Sensor - 23.99 € ● Pressure sensor - 9,60 € ● GPS module - not selected yet sum: 122.60 € + the cost of a GPS module | ● LoStik open source USB LoRa device by Ronoth - 38.92 € ● iFrgoLab LoRa USB gateway - 50.69 € ● Delock USB 10.0m - 15.25 € ● Antenna- value not yet estimated

total sum: 227.46 € + the cost of a GPS module + the cost of antenna

5.3.2. External support
We plan to start our outreach program to get funds, access to equipment and laboratories and also professional technical support.
Our actions will contain following activities:
1. Firstly ask for support in the circle of family, friends and their closest,
2. Secondly we will try to reach sponsors conducting regular activity on different communication channels and social media (details described in next section: “Outreach programme”)
Our goals are to realize following achievements:
- get funds 1000.00 €,
- get access to laboratories and equipments,
- find the experts in mechatronic to ask for review of our ideas.
We got in touch with following institution and hope to improve our relation:
- AGH University of Science and Technology (https://www.agh.edu.pl/) (al. Mickiewicza 30, 30-059 Krakow, Poland)
- Fideltronik Poland Sp. z o.o., (http://fideltronik.com/) Engineering Centre (ul. Cystersów 19, 31-553 Kraków, Poland)

### 6. Outreach programme

We plan to public project status, progress and news at least twice per month.
At present, we have established the website and took care of the logo (presented on the document header) We plan the promotional activities at the school, due to pandemic limitations, remotely.
Our outreach actions performed and media coverage are shown in the picture below (Picture 14).

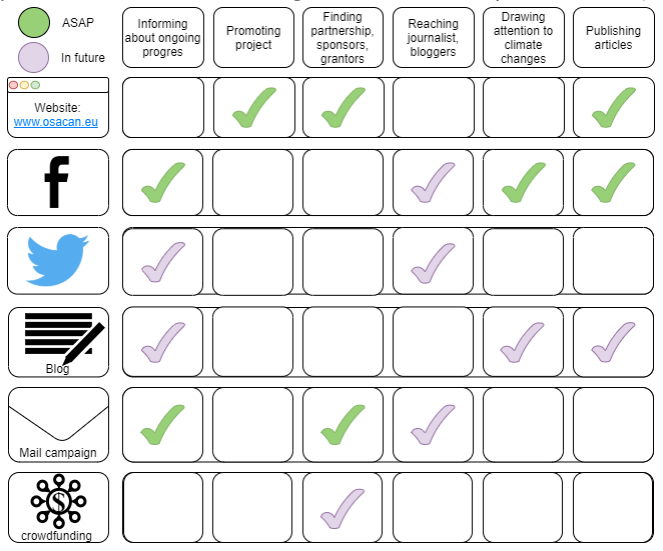
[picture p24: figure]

figure 44

### 7. CANSAT CHARACTERISTICS

Estimated characteristics | Figure
Estimated height of the CanSat (main space) and its parachute (additional space) | 114.4 [mm] - main space 40[mm] - additional space
Diameter of the CanSat | 65.6 [mm]
Mass of the CanSat | 279 [g]
Estimated descent rate | 6 [m/s]
Radio transmitter model and frequency band | SX1278 RA-02 LoRa 433MHz
Estimated time on battery (primary mission) | 5 [h]
Cost of the CanSat | 122.60€

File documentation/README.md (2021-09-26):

   # 📄📄📄
   Here you can find all our documentation created while evaluating OSA.
   
   After FDR we made several changes thus the final OSA description is the (Team_OSATeam_Final)["https://github.com/OSATeam-GitHub/Project-OSA-CanSat-2020-2021/blob/main/documentation/Team_OSATeam_Final.pdf"] file.

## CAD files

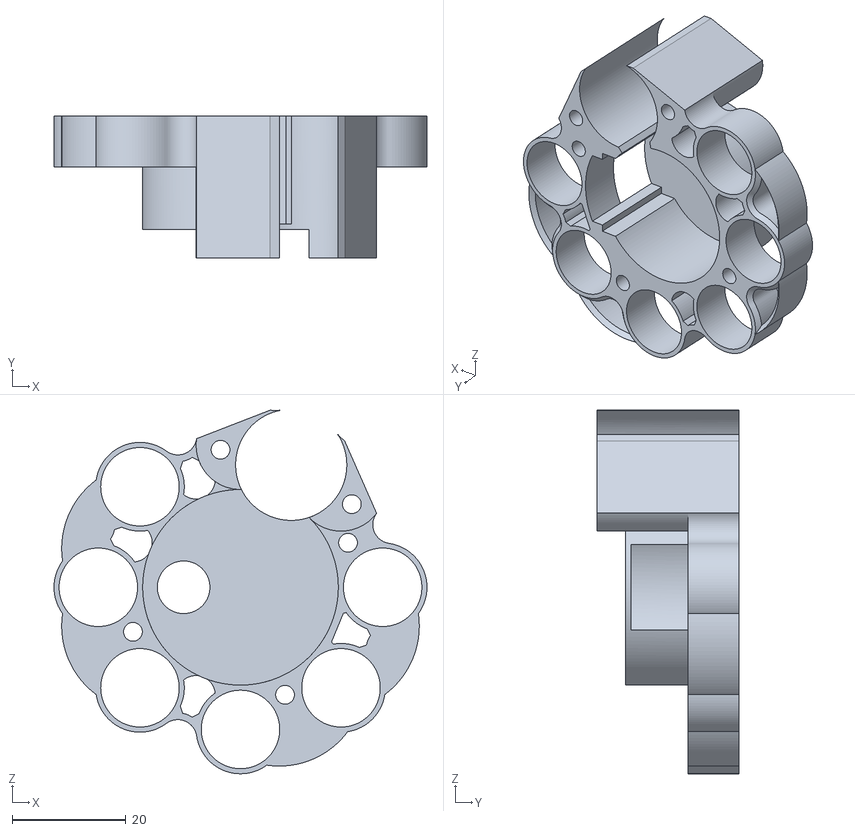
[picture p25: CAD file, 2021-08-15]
hardware/casing and mechanism/base casing part with mechanism/main-base splited/main-base.stl
65.6 x 25.0 x 63.9

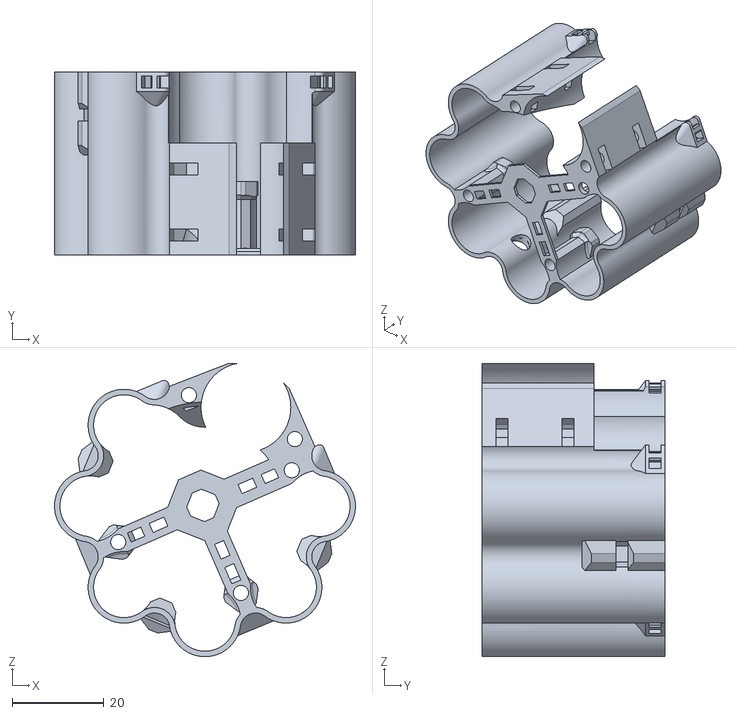
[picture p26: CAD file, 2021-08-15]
hardware/casing and mechanism/main casing/main-mid.stl
65.6 x 39.8 x 63.9

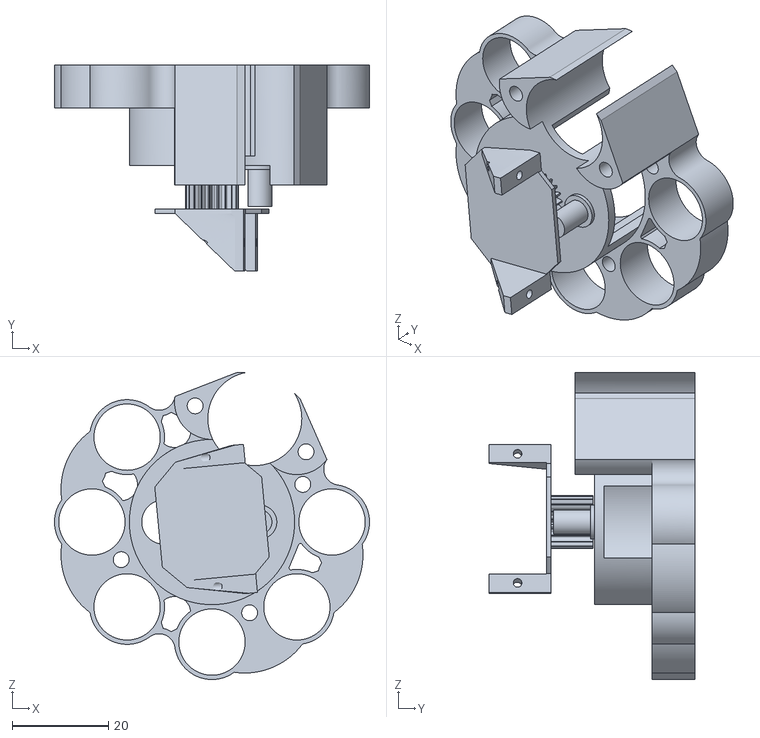
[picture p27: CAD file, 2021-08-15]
hardware/casing and mechanism/base casing part with mechanism/main-base.stl
65.6 x 43.0 x 63.9

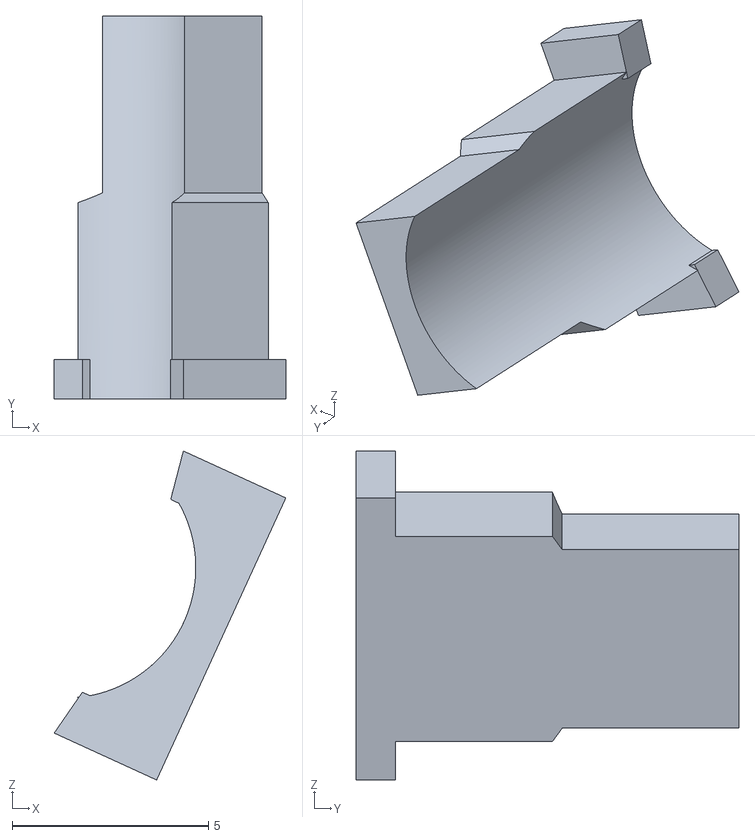
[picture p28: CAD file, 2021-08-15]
hardware/casing and mechanism/base casing part with mechanism/needle mechanizm/blocker.stl
5.90 x 9.75 x 8.38

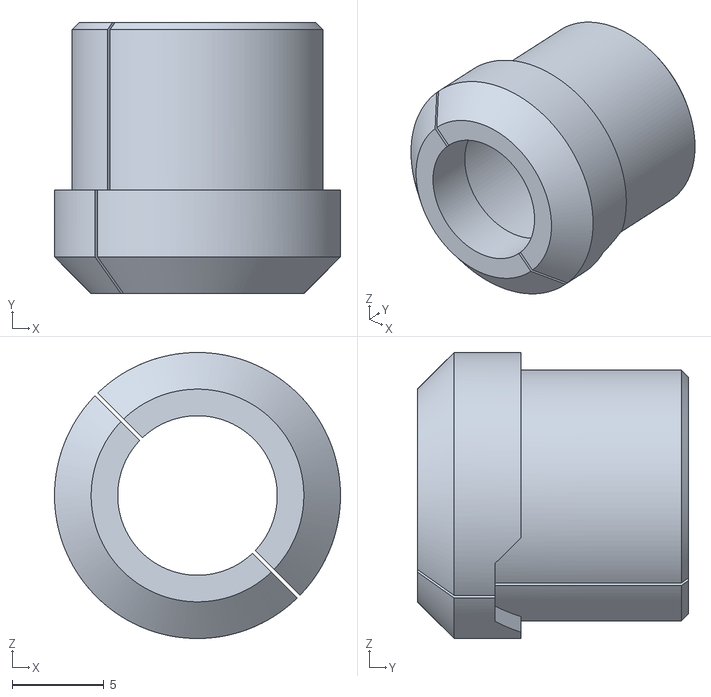
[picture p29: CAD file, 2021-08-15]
hardware/casing and mechanism/base casing part with mechanism/probes adapter with space for screew.stl
15.6 x 14.8 x 15.6

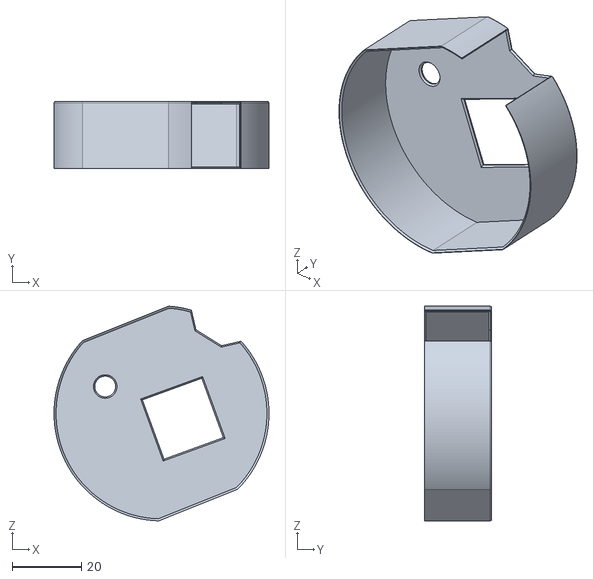
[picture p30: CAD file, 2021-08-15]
hardware/casing and mechanism/electronic case/electronic case.stl
62.2 x 19.4 x 62.1

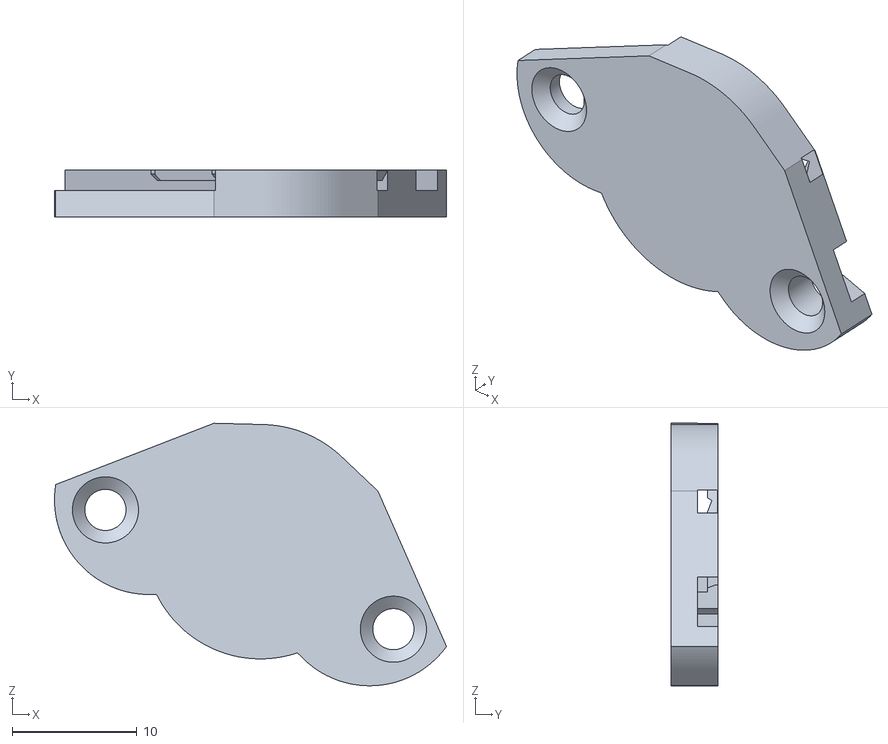
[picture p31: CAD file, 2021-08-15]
hardware/casing and mechanism/main casing/battery lock top.stl
31.4 x 3.80 x 21.1

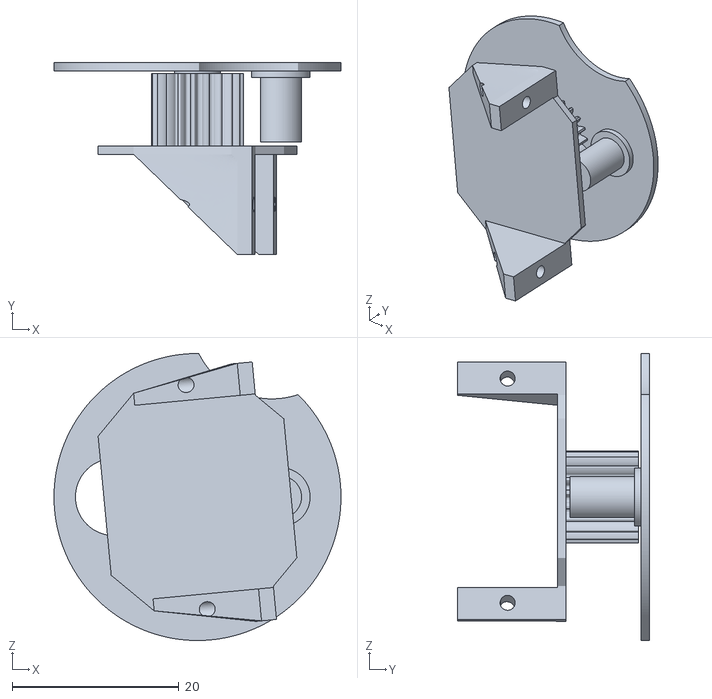
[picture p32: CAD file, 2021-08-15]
hardware/casing and mechanism/base casing part with mechanism/main-base splited/carusele.stl
34.4 x 23.0 x 34.4

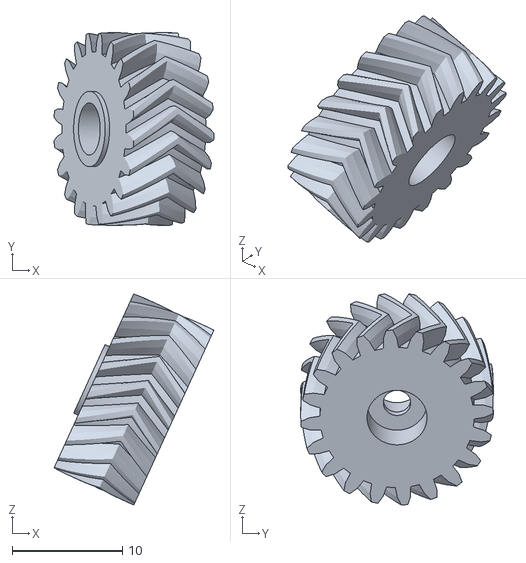
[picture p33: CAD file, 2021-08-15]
hardware/casing and mechanism/base casing part with mechanism/needle mechanizm/motor gear.stl
14.5 x 17.5 x 19.2

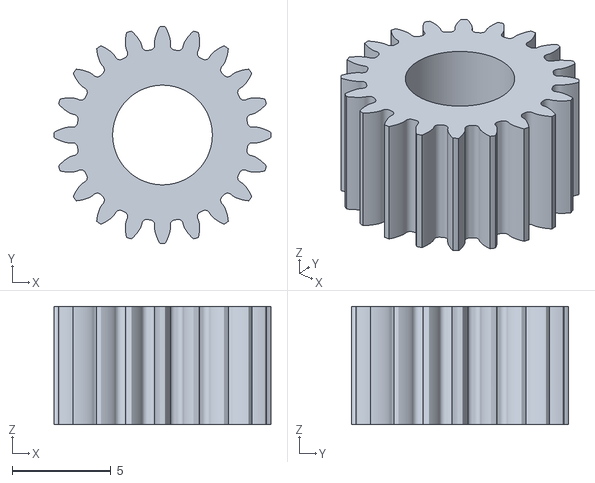
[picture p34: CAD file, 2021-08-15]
hardware/casing and mechanism/base casing part with mechanism/Support gear.stl
11.0 x 11.0 x 6.00

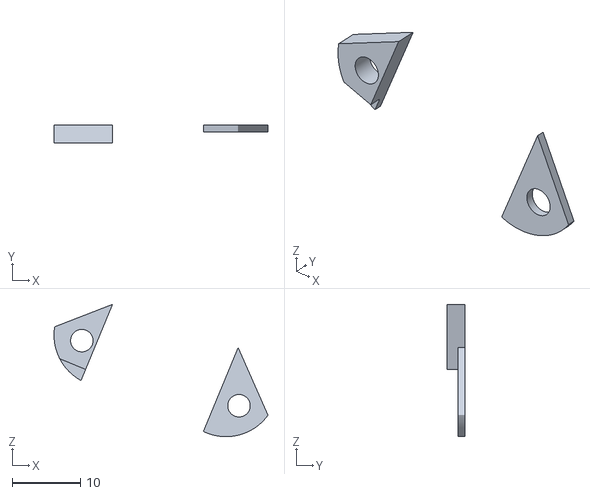
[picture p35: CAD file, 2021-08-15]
hardware/casing and mechanism/main casing/spacers.stl
31.4 x 2.65 x 19.4

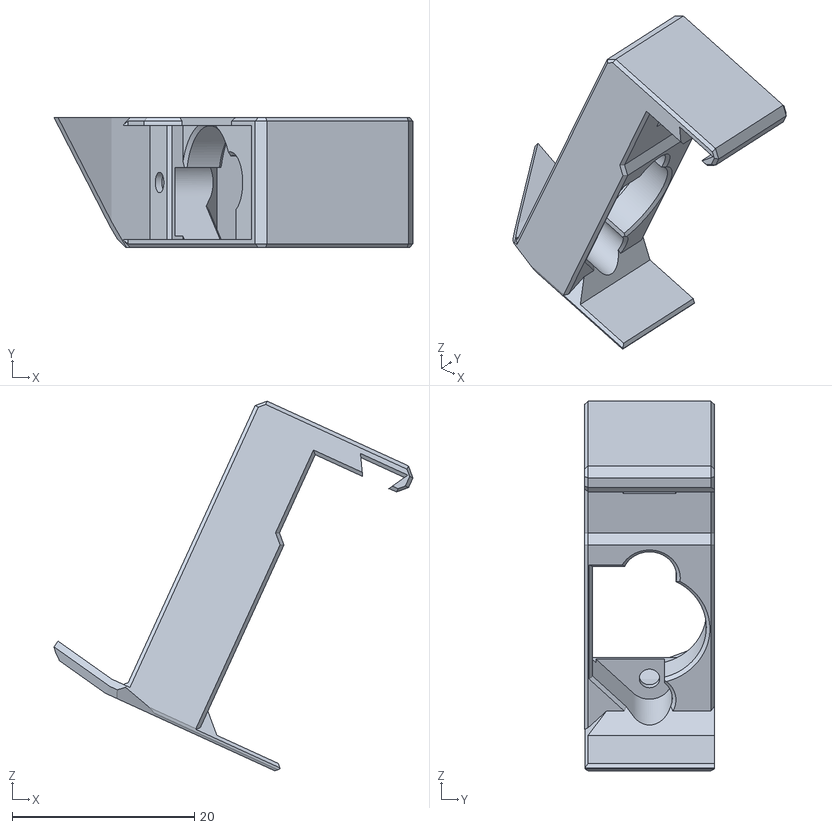
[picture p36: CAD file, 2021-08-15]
hardware/casing and mechanism/base casing part with mechanism/needle mechanizm/mount.stl
39.4 x 14.2 x 40.5

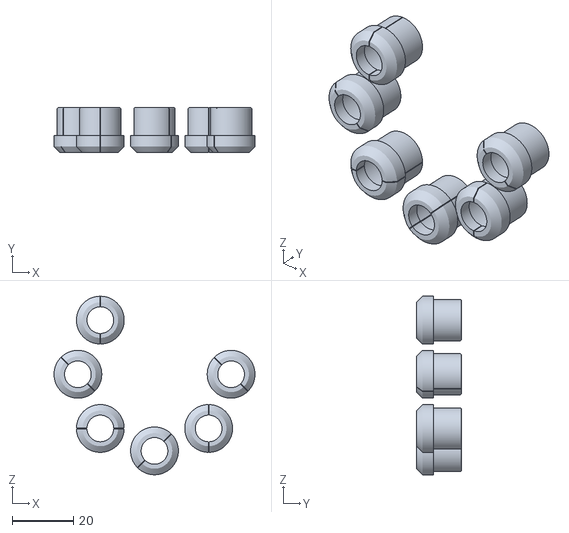
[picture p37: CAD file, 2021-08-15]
hardware/casing and mechanism/base casing part with mechanism/probes adapter.stl
65.6 x 14.8 x 58.3

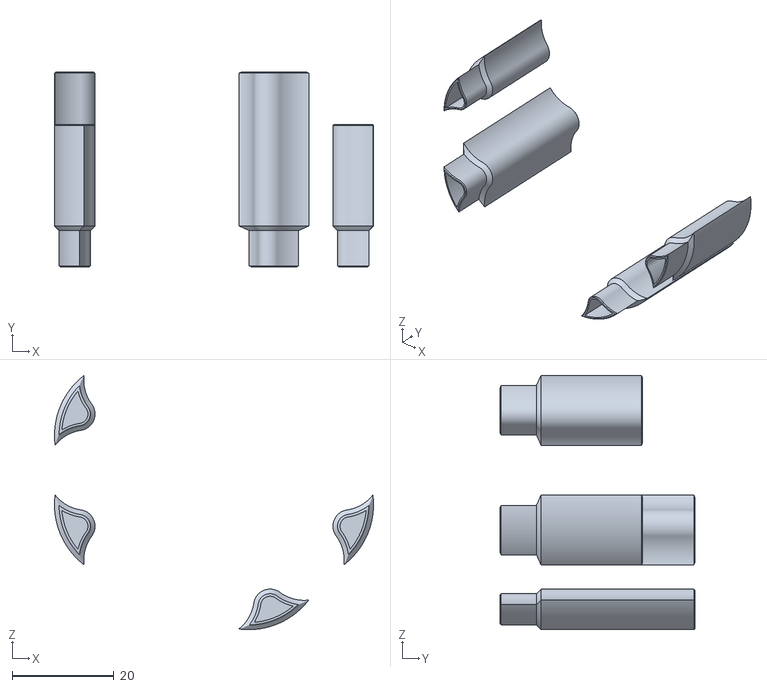
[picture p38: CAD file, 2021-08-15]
hardware/casing and mechanism/main casing/ballast.stl
62.7 x 38.3 x 50.0

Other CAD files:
hardware/casing and mechanism/base casing part with mechanism/needle mechanizm/needle linear.stl
hardware/casing and mechanism/base casing part with mechanism/battery Lock with endstop.stl
hardware/casing and mechanism/base casing part with mechanism/Motor Gear.stl

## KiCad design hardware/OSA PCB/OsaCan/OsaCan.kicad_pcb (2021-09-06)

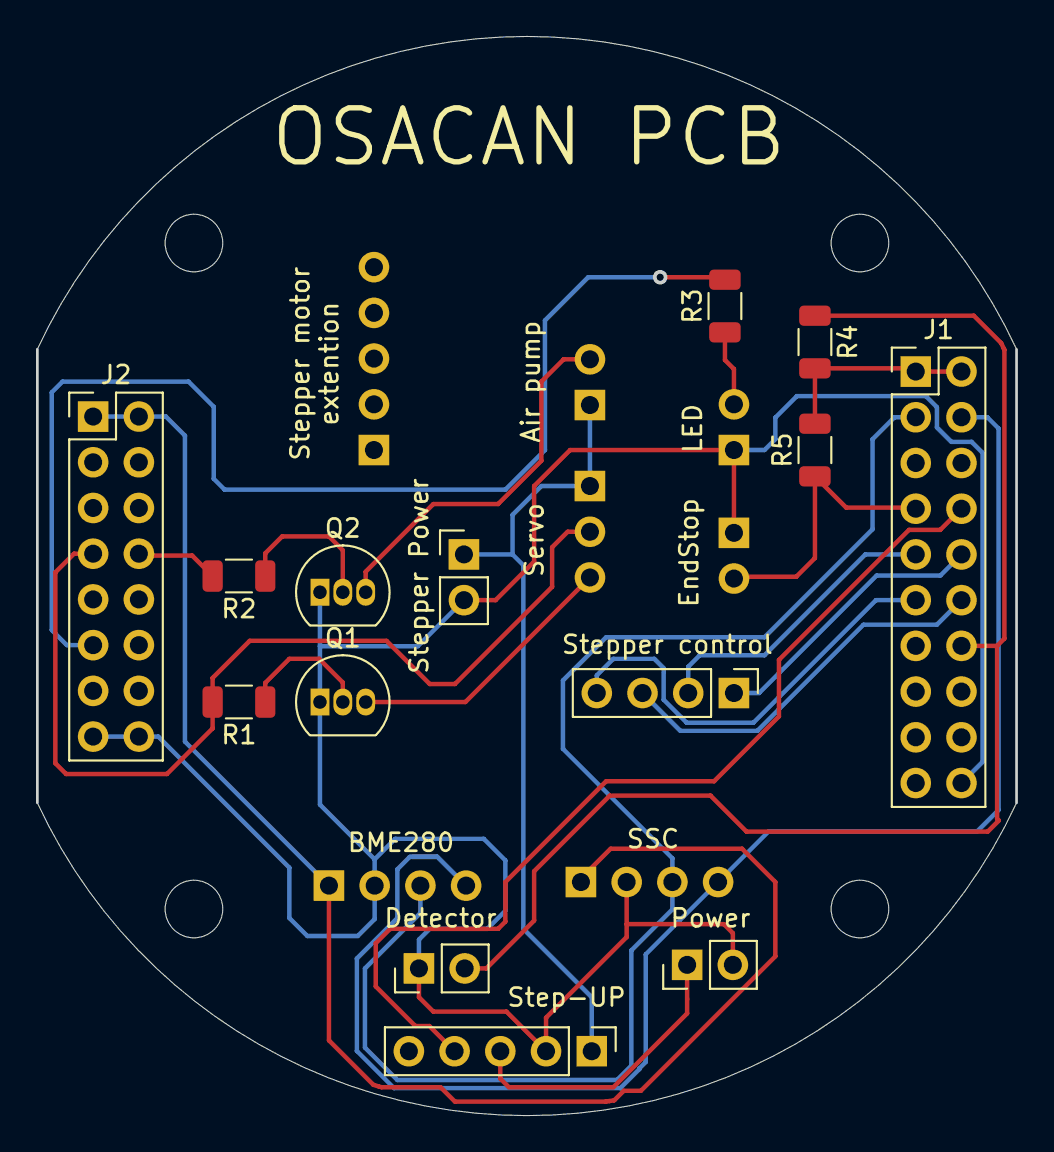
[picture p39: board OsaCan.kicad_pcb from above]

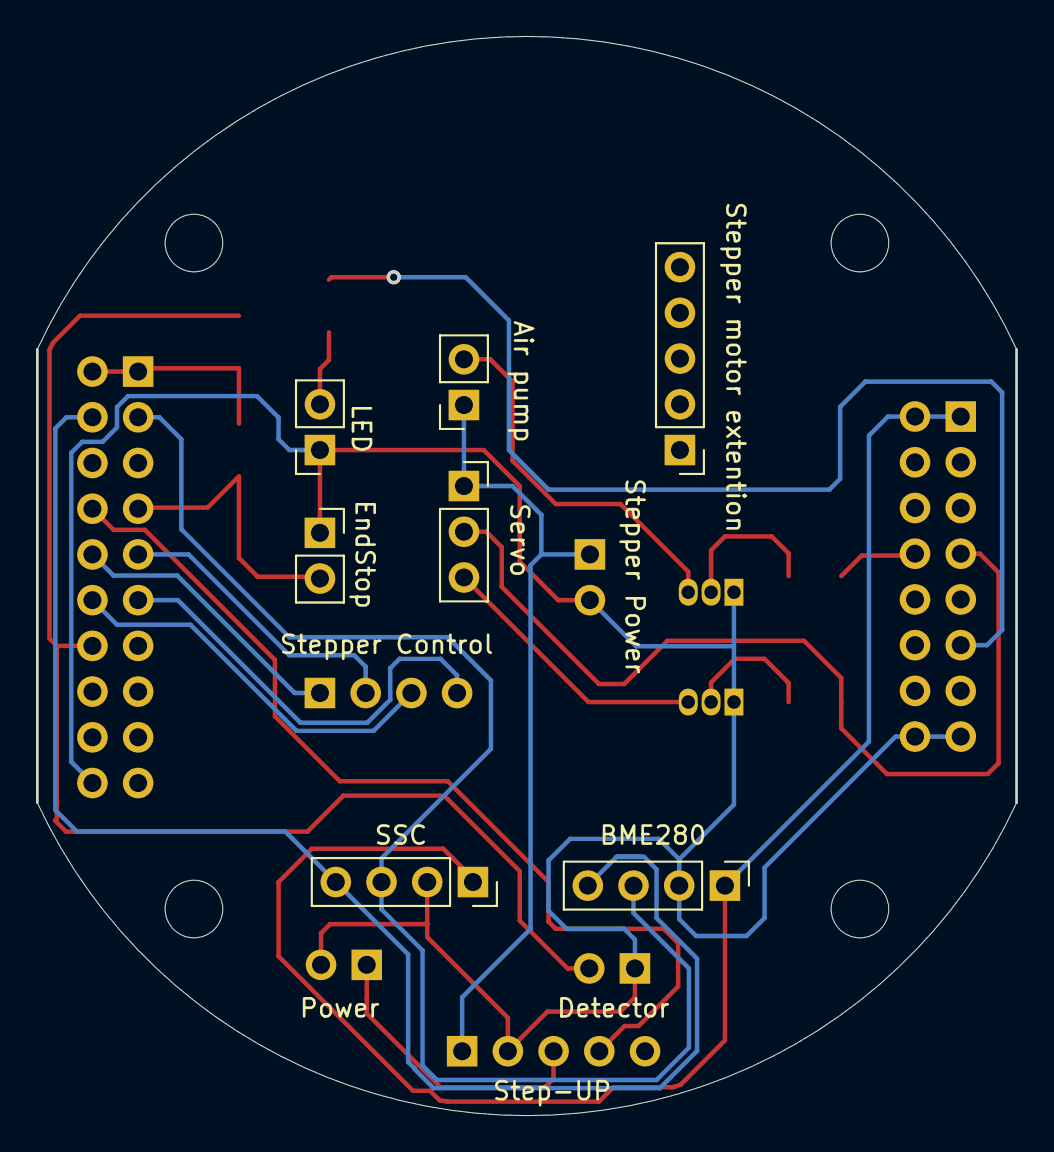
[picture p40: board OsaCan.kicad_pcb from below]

Board: 2 copper layers, 54.4 x 60.0 mm, 21 parts (7 on the bottom side), 22 nets.

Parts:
Air pump: Conn_01x02; PinSocket_1x02_P2.54mm_Vertical
BME280: BME_280; PinHeader_1x04_P2.54mm_Vertical
Detector: Detector; PinHeader_1x02_P2.54mm_Vertical
EndStop: EndStop; PinSocket_1x02_P2.54mm_Vertical
J1: Conn_02x10_Odd_Even; PinHeader_2x10_P2.54mm_Vertical
J2: Conn_02x08_Odd_Even; PinHeader_2x08_P2.54mm_Vertical
LED: Conn_01x02; PinSocket_1x02_P2.54mm_Vertical
Power: POWER; PinHeader_1x02_P2.54mm_Vertical
Q1, Q2: S8050; TO-92_Inline
R1, R2, R3, R4, R5: R; R_1206_3216Metric
SSC: ssc; PinSocket_1x04_P2.54mm_Vertical
Servo: Conn_01x03; PinSocket_1x03_P2.54mm_Vertical
Step-UP: Step-up; PinHeader_1x05_P2.54mm_Vertical
Stepper Power: Stepper Power; PinHeader_1x02_P2.54mm_Vertical
Stepper control: Stepper Motor; PinHeader_1x04_P2.54mm_Vertical
Stepper motor extention: Stepper pin extention; PinHeader_1x05_P2.54mm_Vertical

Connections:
+3V3: BME280.1, J2.1, J2.2, SSC.1
+4V: Power.1, Step-UP.3
+5V: J1.1, J1.2, R4.2, R5.2
+6V: Air pump.1, Servo.1, Step-UP.1, Stepper Power.1
A0: Detector.2, J1.14, R4.1
D0: J1.8, Step-UP.4
D1: EndStop.2, J1.7, R5.1
D2: J1.10, Stepper control.1
D3: J1.9, Stepper control.2
D4: J1.12, Stepper control.3
D5: J1.11, Stepper control.4
D6: J2.7, R1.2, Servo.2
D7: J2.8, R2.2
D13: J2.11, R3.2
GND: BME280.2, Detector.1, EndStop.1, J1.20, J2.15, J2.16, LED.1, Power.2, Q1.1, Q2.1, SSC.2, Step-UP.2, Stepper Power.2
unnamed: Air pump.2, Q2.3
unnamed: LED.2, R3.1
unnamed: Q1.2, R1.1
unnamed: Q1.3, Servo.3
unnamed: Q2.2, R2.1
SCL: BME280.3, J1.3, SSC.3
SDA: BME280.4, J1.4, SSC.4

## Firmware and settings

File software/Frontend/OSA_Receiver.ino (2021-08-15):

/* -----------------------------------------------------------------------
    CANSAT RECEIVER
   ---------------------------------------------------------------------*/

#include <CanSatKit.h>
using namespace CanSatKit;

// ---------------------- SD Card definitions -----------------------------
#include <SD.h>
File dataFile;
String dataFileName = "Rec_7.txt";
int sdCardPin = 11;
// ------------------------------------------------------------------------

// ---------------------- LoRa Radio definitions --------------------------
Radio radio(Pins::Radio::ChipSelect,
            Pins::Radio::DIO0,
            433.300, // frequency in MHz
            Bandwidth_125000_Hz,
            SpreadingFactor_9, //Optimal 9
            CodingRate_4_8);   //Optimal 4_8
// ------------------------------------------------------------------------
//-----------------------------Decoder-------------------------------------
#include "stdio.h"
#include "stdint.h"
#include "string.h"
uint8_t bytes[256];
uint8_t *ptr = bytes;

float res_calcCurrentAltitude;
float res_finalAltitude;
uint8_t res_probesDone[5];
float res_samplesAltuides[5][2];
float res_measurmentCurrentMillis;
uint32_t res_pipePressure;
uint32_t res_ambientPressure;
float res_ambientTemp;
float res_ambientHumidity;
uint8_t res_gpsHours;
uint8_t res_gpsMinutes;
uint8_t res_gpsSeconds;
uint8_t res_gpsDay;
uint8_t res_gpsMonth;
uint16_t res_gpsYear;
uint8_t res_gpsFix;
uint8_t res_gpsFixQuality;
uint8_t res_isParaschuteOpened;
float res_gpsLongitude;
char res_gpsLon;
float res_gpsLatitude;
char res_gpsLat;
float res_gpsAltitude;
uint8_t res_gpsSat;
uint8_t res_programFaze;


// ------------------------------ Other -----------------------------------
bool ledState = false;
const int ledPin = 13;
// ------------------------------------------------------------------------

void setup()
{
    delay(5000);
    SerialUSB.begin(115200);
    SerialUSB.println("CanSat initialization starting...");

    while (!Serial)
        ; // time to get serial running

    if (!SD.begin(sdCardPin))
    {
        SerialUSB.println("the SD Card failed or not present");
        while (1)
        {
        }
    }
    SerialUSB.println("the SD card is started...");

    radio.begin();
    SerialUSB.println("the LoRa radio is started...");

    pinMode(ledPin, OUTPUT);
}

void loop()
{

    // prepare empty space for received frame
    // maximum length is maximum frame length + null termination
    // 255 + 1 byte = 256 bytes
    char dataFrame[256];
    Frame decodedDataFrame;

    digitalWrite(ledPin, ledState);
    ledState = !ledState;

    // receive data and save it to string
    radio.receive(dataFrame);
    for (int i = 0; i < 256; i++)
    {
        bytes[i] = dataFrame[i];
    }

    // get and print signal level (rssi)
    SerialUSB.print("RSSI ;");
    SerialUSB.print(radio.get_rssi_last());
    SerialUSB.print("; DATA ;");

    // print received message
    ptr = bytes;

    ptr = decode_f32(ptr, &res_calcCurrentAltitude);
    ptr = decode_f32(ptr, &res_finalAltitude);
    ptr = decode_uint8(ptr, &res_programFaze);
    for (int i = 0; i < 5; i++)
    {
        ptr = decode_uint8(ptr, &res_probesDone[i]);
    }
    for (int i = 0; i < 5; i++)
    {
        ptr = decode_f32(ptr, &res_samplesAltuides[i][0]);
        ptr = decode_f32(ptr, &res_samplesAltuides[i][1]);
    }
    ptr = decode_f32(ptr, &res_measurmentCurrentMillis);
    ptr = decode_uint32(ptr, &res_pipePressure);
    ptr = decode_uint32(ptr, &res_ambientPressure);
    ptr = decode_f32(ptr, &res_ambientTemp);
    ptr = decode_f32(ptr, &res_ambientHumidity);

    ptr = decode_uint8(ptr, &res_gpsHours);
    ptr = decode_uint8(ptr, &res_gpsMinutes);
    ptr = decode_uint8(ptr, &res_gpsSeconds);

    ptr = decode_uint8(ptr, &res_gpsDay);
    ptr = decode_uint8(ptr, &res_gpsMonth);
    ptr = decode_uint16(ptr, &res_gpsYear);

    ptr = decode_uint8(ptr, &res_gpsFix);
    ptr = decode_uint8(ptr, &res_gpsFixQuality);

    ptr = decode_uint8(ptr, &res_isParaschuteOpened);

    if(res_gpsFix)
    {
        ptr = decode_f32(ptr, &res_gpsLatitude);
    ptr = decode_char(ptr, &res_gpsLat);
    ptr = decode_f32(ptr, &res_gpsLongitude);
    ptr = decode_char(ptr, &res_gpsLon);
    ptr = decode_f32(ptr, &res_gpsAltitude);
    ptr = decode_uint8(ptr, &res_gpsSat);
    }
    
    SerialUSB.print(res_calcCurrentAltitude);    SerialUSB.print(";");
    SerialUSB.print(res_finalAltitude);    SerialUSB.print(";");
    SerialUSB.print(res_programFaze);    SerialUSB.print(";");
    for (int i = 0; i < 5; i++)
    {
    SerialUSB.print(res_probesDone[i]);    SerialUSB.print(";");
    }
    for (int i = 0; i < 5; i++)
    {
    SerialUSB.print(res_samplesAltuides[i][0]);    SerialUSB.print(";");
    SerialUSB.print(res_samplesAltuides[i][1]);    SerialUSB.print(";");
    }
    SerialUSB.print(res_measurmentCurrentMillis);    SerialUSB.print(";");
    SerialUSB.print(res_pipePressure);    SerialUSB.print(";");
    SerialUSB.print(res_ambientPressure);    SerialUSB.print(";");
    SerialUSB.print(res_ambientTemp);    SerialUSB.print(";");
    SerialUSB.print(res_ambientHumidity);    SerialUSB.print(";");
    SerialUSB.print((res_gpsHours, DEC)+2);    SerialUSB.print(":");
    SerialUSB.print(res_gpsMinutes, DEC);    SerialUSB.print(":");
    SerialUSB.print(res_gpsSeconds, DEC);    SerialUSB.print(";");
    SerialUSB.print(res_gpsDay, DEC);    SerialUSB.print("/");
    SerialUSB.print(res_gpsMonth, DEC);    SerialUSB.print("/");
    SerialUSB.print(res_gpsYear, DEC);    SerialUSB.print(";");
    SerialUSB.print(res_gpsFix);    SerialUSB.print(";");
    SerialUSB.print(res_gpsFixQuality);    SerialUSB.print(";");
    SerialUSB.print(res_isParaschuteOpened);    SerialUSB.print(";");
    if(res_gpsFix>0)
    {
    SerialUSB.print(res_gpsLatitude);//    SerialUSB.print(";");
    SerialUSB.print(res_gpsLat);    SerialUSB.print(";");
    SerialUSB.print(res_gpsLongitude);//    SerialUSB.print(";");
    SerialUSB.print(res_gpsLon);    SerialUSB.print(";");
    SerialUSB.print(res_gpsAltitude);    SerialUSB.print(";");
    SerialUSB.print(res_gpsSat);
    SerialUSB.println();
    }
    else
    {
        SerialUSB.println();
    }
     decodedDataFrame.print(res_calcCurrentAltitude);    decodedDataFrame.print(";");
     decodedDataFrame.print(res_finalAltitude);    decodedDataFrame.print(";");
     decodedDataFrame.print(res_programFaze);    decodedDataFrame.print(";");

    for(int i = 0; i<5;i++)
    {
        decodedDataFrame.print(res_probesDone[i]);    decodedDataFrame.print(";");
    }
    for(int i = 0; i<5;i++)
    {
        decodedDataFrame.print(res_samplesAltuides[i][0]);    decodedDataFrame.print(";");
        decodedDataFrame.print(res_samplesAltuides[i][1]);    decodedDataFrame.print(";");

    }
    decodedDataFrame.print(res_measurmentCurrentMillis);    decodedDataFrame.print(";");
    decodedDataFrame.print(res_pipePressure);    decodedDataFrame.print(";");
    decodedDataFrame.print(res_ambientPressure);    decodedDataFrame.print(";");
    decodedDataFrame.print(res_ambientTemp);    decodedDataFrame.print(";");
    decodedDataFrame.print(res_ambientHumidity);    decodedDataFrame.print(";");
    decodedDataFrame.print(res_gpsHours);    decodedDataFrame.print(";");
    decodedDataFrame.print(res_gpsMinutes);    decodedDataFrame.print(";");
    decodedDataFrame.print(res_gpsSeconds);    decodedDataFrame.print(";");
    decodedDataFrame.print(res_gpsDay);    decodedDataFrame.print(";");
    decodedDataFrame.print(res_gpsMonth);    decodedDataFrame.print(";");
    decodedDataFrame.print(res_gpsYear);    decodedDataFrame.print(";");
    decodedDataFrame.print(res_gpsFix);    decodedDataFrame.print(";");
    decodedDataFrame.print(res_gpsFixQuality);    decodedDataFrame.print(";");
    decodedDataFrame.print(res_isParaschuteOpened);    decodedDataFrame.print(";");
    if(res_gpsFix>0)
    {
    decodedDataFrame.print(res_gpsLatitude);
    decodedDataFrame.print(res_gpsLat);    decodedDataFrame.print(";");
    decodedDataFrame.print(res_gpsLongitude);
    decodedDataFrame.print(res_gpsLon);    decodedDataFrame.print(";");
    decodedDataFrame.print(res_gpsAltitude);    decodedDataFrame.print(";");
    decodedDataFrame.print(res_gpsSat);
    decodedDataFrame.println();
    }

    //SerialUSB.print(dataFrame);
    // open the file. note that only one file can be open at a time,
    // so you have to close this one before opening another.
   dataFile = SD.open(dataFileName, FILE_WRITE);

    // if the file is available, write to it:
    if (dataFile)
    {
        dataFile.print(decodedDataFrame);
        dataFile.close();
    }
    // if the file isn't open, pop up an error:
    else
    {
        SerialUSB.println("error opening datalog.txt");
    }
}

uint8_t *encode_bytes(uint8_t *ptr, void *bytes, uint16_t size)
{
    memcpy(ptr, bytes, size);
    return ptr + size;
}

uint8_t *decode_bytes(uint8_t *ptr, void *bytes, uint16_t size)
{
    memcpy(bytes, ptr, size);
    return ptr + size;
}

uint8_t *encode_uint8(uint8_t *ptr, uint8_t value)
{
    return encode_bytes(ptr, &value, sizeof(uint8_t));
}

uint8_t *encode_uint16(uint8_t *ptr, uint16_t value)
{
    return encode_bytes(ptr, &value, sizeof(uint16_t));
}

uint8_t *encode_uint32(uint8_t *ptr, uint32_t value)
{
    return encode_bytes(ptr, &value, sizeof(uint32_t));
}

uint8_t *encode_f32(uint8_t *ptr, float value)
{
    return encode_bytes(ptr, &value, sizeof(float));
}

uint8_t *decode_uint8(uint8_t *ptr, uint8_t *value)
{
    return decode_bytes(ptr, value, sizeof(uint8_t));
}

uint8_t *decode_uint16(uint8_t *ptr, uint16_t *value)
{
    return decode_bytes(ptr, value, sizeof(uint16_t));
}

uint8_t *decode_uint32(uint8_t *ptr, uint32_t *value)
{
    return decode_bytes(ptr, value, sizeof(uint32_t));
}

uint8_t *decode_f32(uint8_t *ptr, float *value)
{
    return decode_bytes(ptr, value, sizeof(float));
}
uint8_t *decode_char(uint8_t *ptr, char *value)
{
    return decode_bytes(ptr, value, sizeof(char));
}
uint8_t *encode_char(uint8_t *ptr, char value)
{
    return encode_bytes(ptr, &value, sizeof(char));
}

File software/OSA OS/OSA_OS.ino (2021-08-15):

#include <CanSatKit.h>
/* -----------------------------------------------------------------------
 *  CANSAT TRANSMITTER
 * ---------------------------------------------------------------------*/
#include <OsaCarusele.h>
#include <Adafruit_GPS.h>

using namespace CanSatKit;
//unsigned long symulacjaCurrentMillis, symulacjaPreviousMillis;
unsigned long sampleCurrentMillis =0 , samplePreviousMillis = 0, sampleTimeInterval;
//int symulacjaAltitude;

OsaCarusele cansat;
void setup()
{
  cansat.begin();
  //symulacjaCurrentMillis = 0;
  //symulacjaPreviousMillis = 0;
  //symulacjaAltitude = 0;

  cansat.autohome();  cansat.programFaze = 1;
  delay(1000); //dojeżdża do krańcówki
  cansat.rest();  cansat.programFaze = 2;
  delay(500);
  cansat.backlashCorrection(0);

  //cansat.initialAltitude = symulacjaAltitude;
  cansat.initialAltitude = cansat.altiduteCalc();
  cansat.finalAltitude = cansat.initialAltitude;
  cansat.currentAltitude = cansat.initialAltitude;
}

void loop()
{
  SerialUSB.println("Gotowy do lotu "); cansat.programFaze = 3;
  while (!cansat.isParachuteOpened()) // -> sprawdza kiedy mniej więcej otworzy się spadochron i po 30 m spadaku wychodzi z pętli
  {
   // cansat.gpsCheck();
    cansat.ifIntervalSendMeasurments();
  }
  cansat.currentMillis = millis();
  cansat.previousMillis = cansat.currentMillis;
  while (cansat.currentMillis - cansat.previousMillis < 200)
  {
    cansat.ifIntervalSendMeasurments();
    cansat.currentMillis = millis();
  }
  cansat.programFaze = 4;
  cansat.finalAltitude = cansat.altiduteCalc();
  if((cansat.finalAltitude<0)||(cansat.finalAltitude>600))
    {
      cansat.finalAltitude = 150;
      cansat.programFaze = 5;
    }

 // cansat.finalAltitude = 150; //symulacja

  SerialUSB.println("zaczynam spaaaaadać!!!");
 // SerialUSB.print("Maksymalna wysokość: ");
  //SerialUSB.println(finalAltitude);
  cansat.leaveRest();cansat.programFaze = 6;

  SerialUSB.println("wykonałem leaveRest, zaczynam misje, pozycja silnika: ");
  //SerialUSB.println(cansat.stepper_position); //igła przygotowana do pobierania próbek
  nmea_float_t probesAltitudeInterval = ((cansat.finalAltitude - 2) - cansat.initialAltitude) / 5;
  cansat.previousAltitude = (cansat.finalAltitude - 2) + probesAltitudeInterval;
  int probesIndex = 0;
  sampleTimeInterval = probesAltitudeInterval/10;  

  while (probesIndex < 5)
  {
    //symulacjaCurrentMillis = millis();

    cansat.ifIntervalSendMeasurments();
    //cansat.currentAltitude = symulacjaAltitude;
    cansat.currentAltitude = cansat.altiduteCalc();
    sampleCurrentMillis = millis();
    if ((cansat.currentAltitude <= cansat.previousAltitude - probesAltitudeInterval)&&(sampleCurrentMillis >= samplePreviousMillis + sampleTimeInterval))
    {
      cansat.programFaze = probesIndex;
      cansat.previousAltitude = cansat.currentAltitude;
      samplePreviousMillis = sampleCurrentMillis;
      cansat.takeSample(probesIndex);
      probesIndex++;
    }

    /*if (symulacjaCurrentMillis > symulacjaPreviousMillis + 1000)
    {
      symulacjaPreviousMillis = symulacjaCurrentMillis;
      symulacjaAltitude -= 7;
    }*/
  }
  cansat.programFaze =7;
  cansat.repidProbes();
  cansat.programFaze = 8;
  SerialUSB.println("Pobrałem ostatnia probowke, wykonuje rest");

  cansat.rest();
  cansat.programFaze = 9;
  digitalWrite(cansat.STEPUPPOWER, LOW);
  while (1)
  {
    cansat.ifIntervalSendMeasurments();
  }
}
